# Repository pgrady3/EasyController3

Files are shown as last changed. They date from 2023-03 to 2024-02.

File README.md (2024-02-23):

# EasyController3

*Update Feb 23, 2024 - The EasyController 3.2 has been released, which has been more thoroughly tested than the 3.0. Further tutorial videos and build guides are coming!*

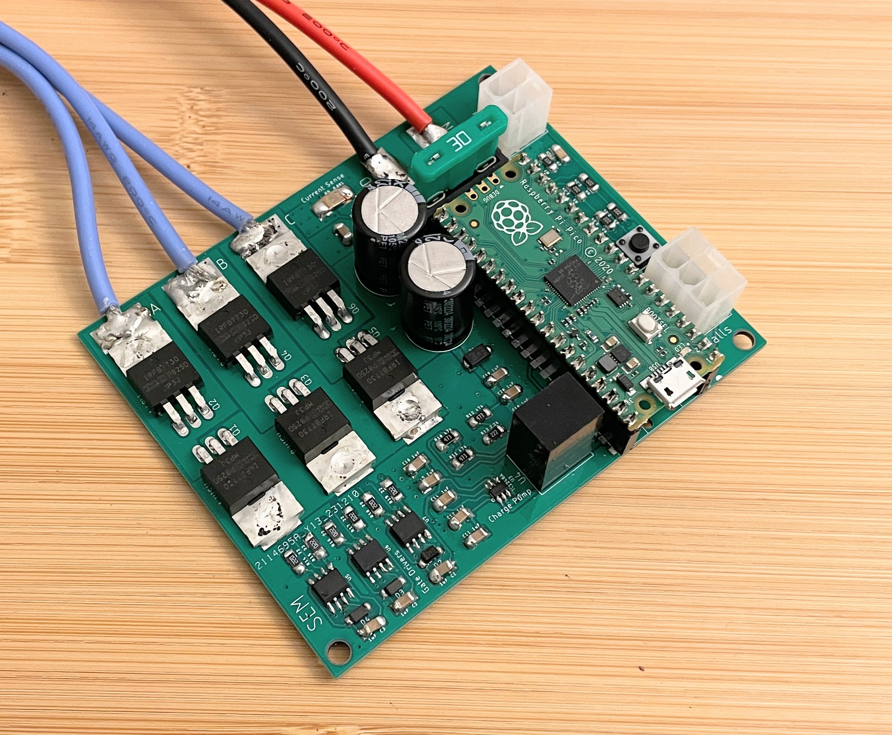
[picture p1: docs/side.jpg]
Assembled Controller


The EasyController3 is the next evolution of the successful [EasyController2](https://github.com/pgrady3/EasyController2). The new version is cheaper, more efficient, and uses well-stocked components.

## Improvements over the EasyController2

* Reduced BOM cost from $70 to $43
* Uses more efficient synchronous PWM. Greater efficiency under partial throttle operation
* Improved from duty-cycle control to torque-control, improving controllability and reducing current spikes
* Added regenerative braking
* Lowered quiescent power from 960 mW to 280 mW in a typical installation
* Based on Raspberry Pi Pico microcontroller
* Uses more widely available surface-mount components

## Getting Started

For a comprehensive guide on how to build your own EasyController, please see the [getting started guide](/docs/getting-started.md).

## Background

The EasyController3 is a a simple brushless (BLDC) sensored motor controller (also known as an ESC, motor inverter, or motor drive). It is intended to power vehicles such as electric bikes, skateboards, or [Eco-Marathon vehicles](https://en.wikipedia.org/wiki/Shell_Eco-marathon) in the 50-1000 watt range. It is designed for hobbyists to assemble at home.

The EasyController family was built to to fill a gap in publicly released motor controller designs. It is designed to be simple yet still highly functional. It deliberately omits more complex features such as sensorless or field-oriented control, however these features can be added with modification. This project is meant as a learning tool and a foundation to potentially build more complex designs from.

## Specifications
* 8v-60v operation
* 20A continuous current, 40A burst (more with heatsinking)
* Large surface mount components designed to be hand-soldered by hobbyists
* Socket for automotive fuse
* Automatic hall sensor identification
* Simple, well-documented code. <400 lines with comments
* Torque or duty-cycle control
* Raspberry Pi Pico microcontroller, compatible with Windows/Mac/Linux
* DGD2304 gate drivers
* IRFB7730 MOSFETS
* BOM cost of $43 USD
* Open source under MIT License

## Schematic

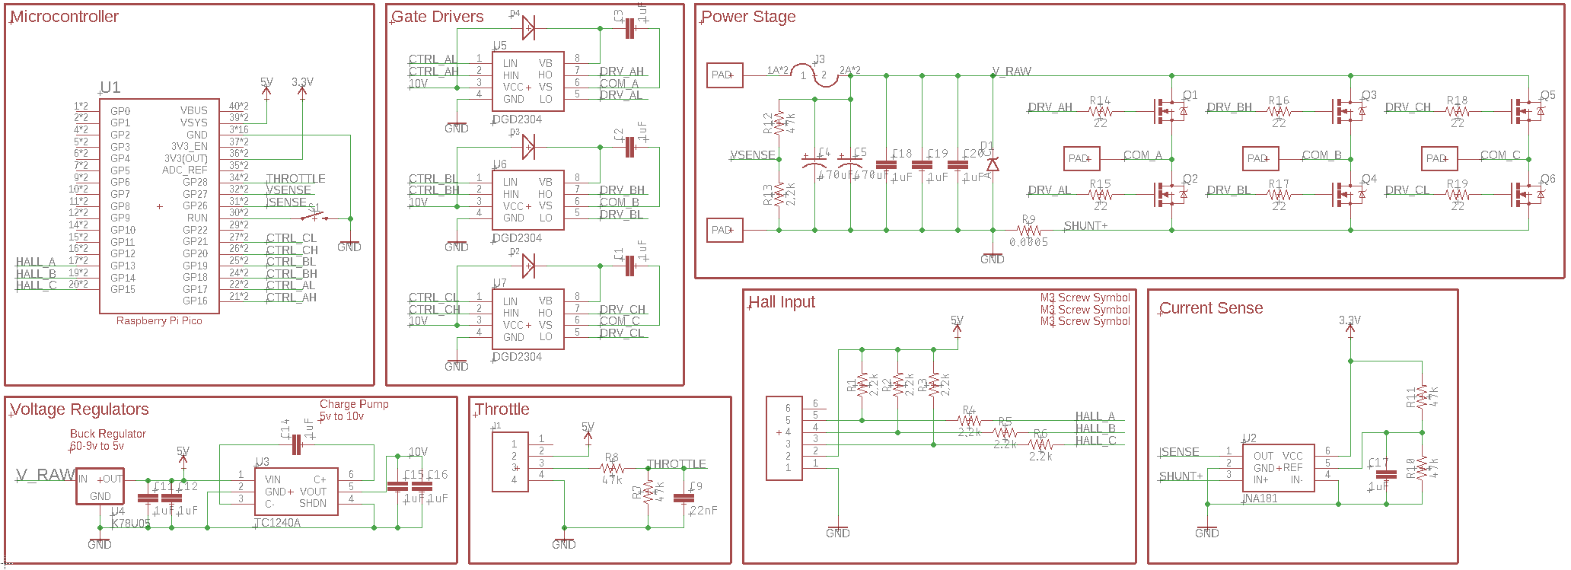
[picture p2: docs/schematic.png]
Schematic


## Board

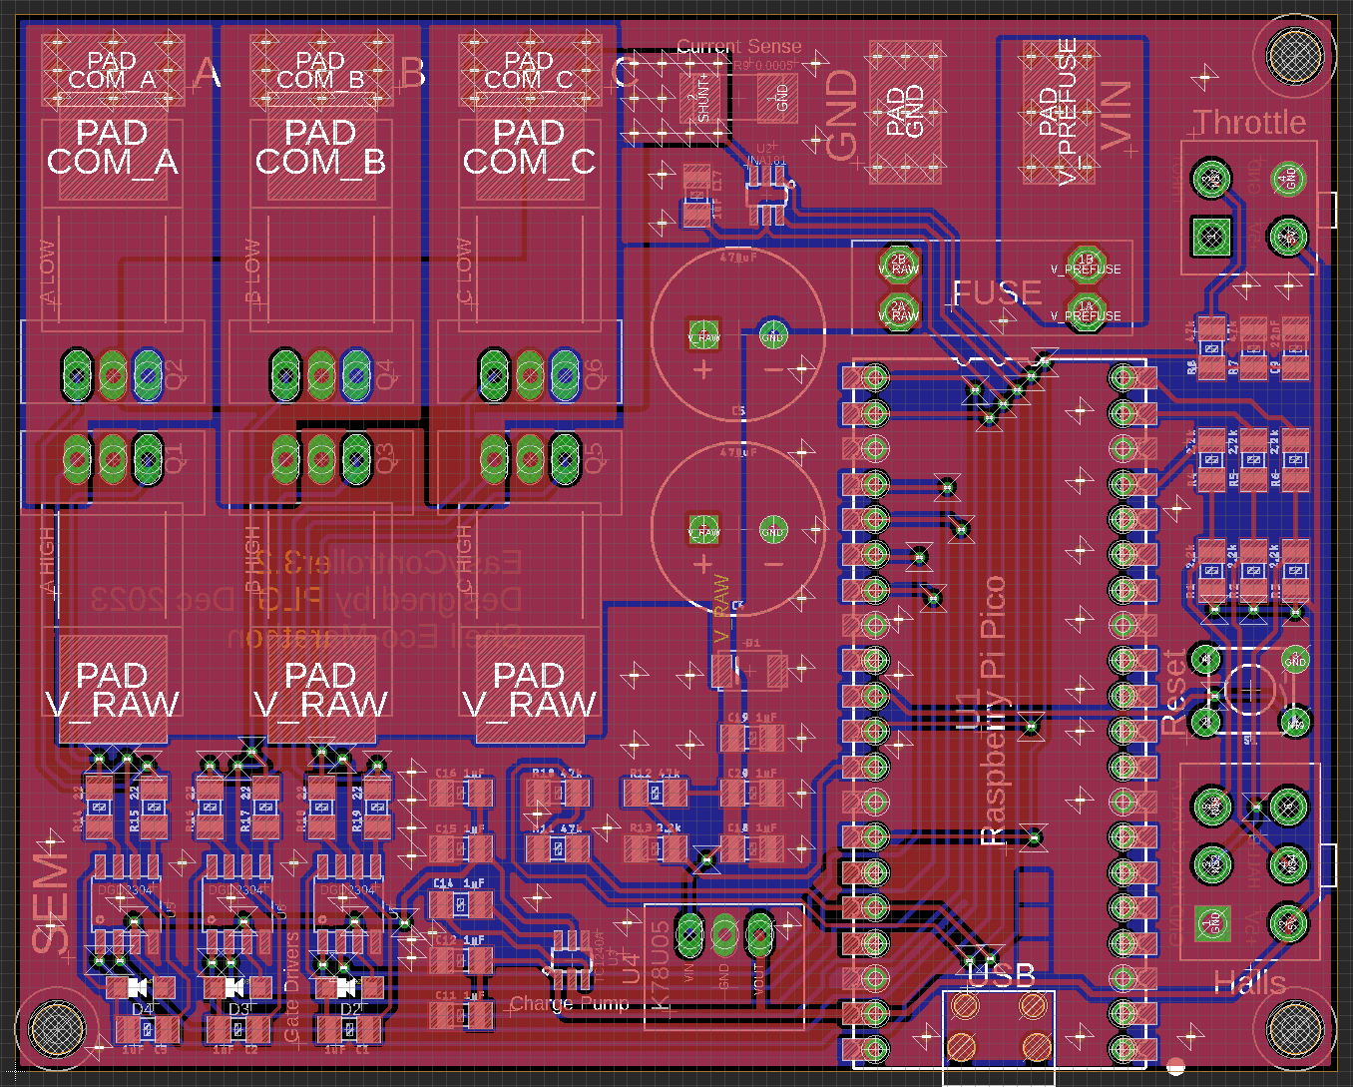
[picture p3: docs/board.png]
Board
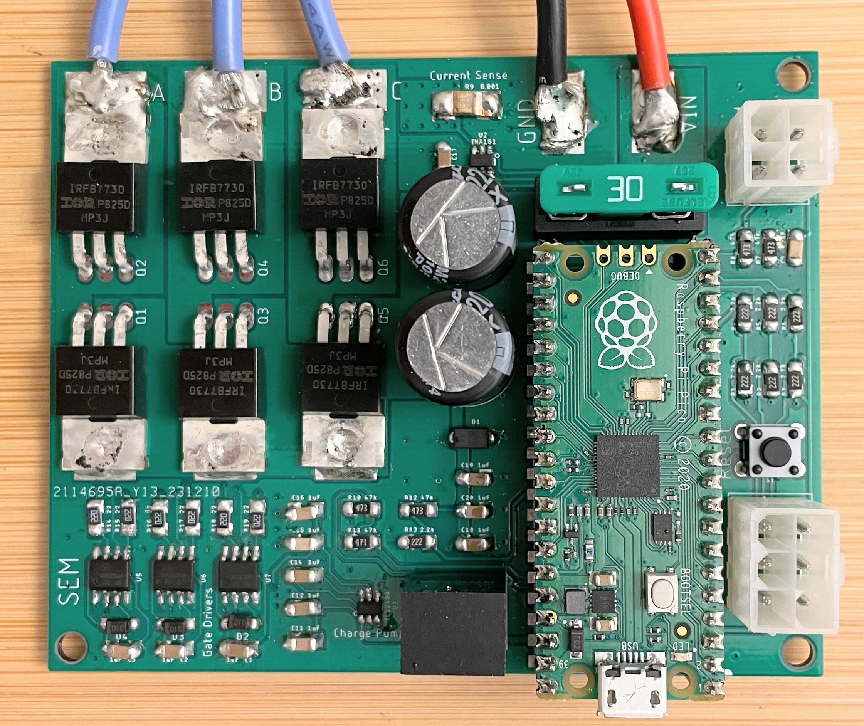
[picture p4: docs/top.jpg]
 

## Software Used

* PCB layout: [Eagle](https://www.autodesk.com/products/eagle/free-download)
* Compiler: [RP2040 C SDK](https://datasheets.raspberrypi.com/pico/getting-started-with-pico.pdf) (see chapter 9)

## Other Related Controller Designs

There are several other open-source motor controller designs worth mentioning:
* The [VESC](https://vesc-project.com/) is a highly capable design, and is well suited for vehicle applications. However, due to the complexity and poorly written code, it is difficult to modify.
* The [Simple FOC](https://simplefoc.com/) project is an open-source library for FOC commutation. However, due to the hardware-agnostic code, it is low-performance and suited for gimbal motors, not vehicle applications.
* The [ODrive](https://odriverobotics.com/) is a modular controller built for robotics applications. However, the hardware is closed-source.

The EasyController3 is most suitable for people who want to design, build, and understand their own motor controller. If you'd just like to purchase something off-the-shelf, we recommend the VESC, which is around $100 USD.

## Contact Us

This controller was designed by [Patrick Grady](https://www.pgrady.net/), formerly with [Duke Electric Vehicles](https://www.duke-ev.org/). If you have a question that other users may also have, please open a GitHub issue. Alternatively, the best way to reach me is by email, at (first name).(last name)@outlook.com.

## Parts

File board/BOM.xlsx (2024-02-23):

Digikey Part # | Mfg Part # | Description | Qty | Cost | Line Cost | Designator | Total Cost
2648-SC0915CT-ND | SC0915 | Raspberry Pi Pico | 1 | 4 | 4 | U1 | 43.15
IRFB7730PBF-ND | IRFB7730PBF | Power FETs | 6 | 3.25 | 19.5 | Q1,Q2,Q3,Q4,Q5,Q6
DGD2304S8-13DICT-ND | DGD2304S8-13 | Gate driver | 3 | 1.26 | 3.78 | U5,U6,U7
SMD110PL-TPMSCT-ND | SMD110PL-TP | Diode for gate driver | 3 | 0.25 | 0.75 | D2,D3,D4
296-INA181A1QDBVRQ1CT-ND | INA181A1 | Current shunt amplifier | 1 | 0.58 | 0.58 | U2
4506-EBWM2512FL500S9CT-ND | EBWM2512FL500S9 | Current shunt resistor | 1 | 0.63 | 0.63 | R9
TC1240AECHCT-ND | TC1240AECHTR | Charge pump IC | 1 | 1.11 | 1.11 | U3
2725-K78U05-500R3-ND | K78U05-500R3 | 5V buck regulator | 1 | 2.89 | 2.89 | U4
1189-3684-ND | 100PX220MEFC12.5X20 | 220uF Capacitor | 2 | 1.14 | 2.28 | C4,C5
SMAJ60CALFCT-ND | SMAJ60CA | TVS Diode | 1 | 0.47 | 0.47 | D1
RMCF1206JT47K0CT-ND | RMCF1206JT47K0 | 47k Resistor | 5 | 0.03 | 0.15 | R7,R8,R10,R11,R12
RMCF1206JT2K20CT-ND | RMCF1206JT2K20 | 2.2k Resistor | 7 | 0.03 | 0.21 | R1,R2,R3,R4,R5,R6,R13
RMCF1206JT22R0CT-ND | RMCF1206JT22R0 | 22 Resistor | 6 | 0.03 | 0.18 | R14,R15,R16,R17,R18,R19
478-12061C223KAT4ACT-ND | 12061C223KAT4A | 22nF Capacitor | 1 | 0.08 | 0.08 | C9
1276-1838-1-ND | CL31B105KCHNNNE | 1uF Capacitor | 13 | 0.19 | 2.47 | C1,C2,C3,C11,C12,C13,C14,C15,C16,C17,C18,C19,C20
36-3557-2-ND | 3557-2 | Fuse holder | 1 | 1.33 | 1.33 | J3
450-1650-ND | 1825910-6 | Reset pushbutton | 1 | 0.13 | 0.13 | S1
A30603-ND | 1586037-4 | 4 pin female VAL-U-LOK | 1 | 0.68 | 0.68 | J1
A30604-ND | 1586037-6 | 6 pin female VAL-U-LOK | 1 | 0.65 | 0.65 | J2
A30591-ND | 794954-4 | 4 pin male VAL-U-LOK | 1 | 0.21 | 0.21
A30592-ND | 794954-6 | 6 pin male VAL-U-LOK | 1 | 0.24 | 0.24
A99267CT-ND | 794956-1 | Crimp pin VAL-U-LOK | 10 | 0.05 | 0.5
F4202-ND | 0287030.PXCN | 30A fuse | 1 | 0.33 | 0.33

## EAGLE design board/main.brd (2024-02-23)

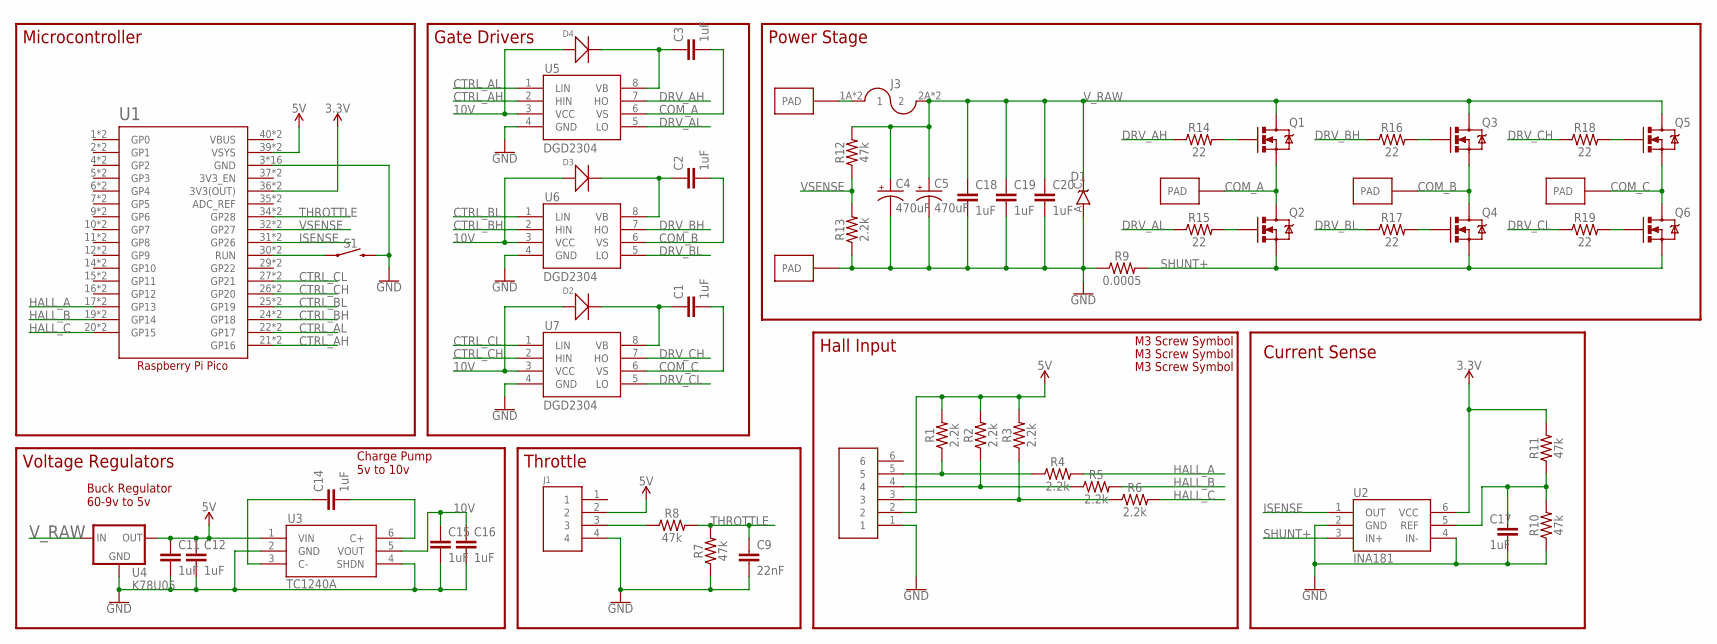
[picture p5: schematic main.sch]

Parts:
C1, C2, C3, C11, C12, C14, C15, C16, C17, C18, C19, C20: 1uF; 1206
C4, C5: 470uF; CPOL-RADIAL-5MM-10MM
C9: 22nF; 1206
D1: TVS; DO-214AC
D2, D3, D4: SMD-DIODE-100V-200MA(SOD-123); SOD-123
J1: HEADER4VALULOK; 4PINVALULOK
J2: HEADER6; 6PINVALULOK
J3: FUSE; AUTO_FUSE
Q1, Q2, Q3, Q4, Q5, Q6: MOSFET-NCHANNELTO-220-FLAT; TO-220-FLAT
R1, R2, R3, R4, R5, R6, R13: 2.2k; 1206
R7, R8, R10, R11, R12: 47k; 1206
R9: 0.0005; R2512
R14, R15, R16, R17, R18, R19: 22; 1206
S1: MOMENTARY-SWITCH-SPST-PTH-6.0MM; TACTILE_SWITCH_PTH_6.0MM
U1: RASPBERRY_PICO-NO_DEBUG; PICO-PKG-NO_DEBUG
U2: INA181; SOT23-6
U3: TC1240A; SOT23-6
U4: K78U05; V78W_BACKWARDS
U5, U6, U7: DGD2304; SOIC8
U$4, U$5, U$6, U$7, U$8: PAD
U$10, U$11, U$12: SCREW; M3HOLE

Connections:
3.3V: R11.2, U1.36 (3V3(OUT)), U1.P$36 (3V3(OUT)), U2.6 (VCC)
5V: C11.1, C12.1, J1.2, J2.2, R1.2, R2.2, R3.2, U1.39 (VSYS), U1.P$39 (VSYS), U3.1 (VIN), U4.OUT
10V: C15.1, C16.1, D2.+, D3.+, D4.+, U3.5 (VOUT), U5.3 (VCC), U6.3 (VCC), U7.3 (VCC)
COM_A: C3.2, Q1.3 (S), Q2.2 (D), Q2.PAD (D), U5.6 (VS), U$6.PAD
COM_B: C2.2, Q3.3 (S), Q4.2 (D), Q4.PAD (D), U6.6 (VS), U$7.PAD
COM_C: C1.2, Q5.3 (S), Q6.2 (D), Q6.PAD (D), U7.6 (VS), U$8.PAD
CTRL_AH: U1.21 (GP16), U1.P$21 (GP16), U5.2 (HIN)
CTRL_AL: U1.22 (GP17), U1.P$22 (GP17), U5.1 (LIN)
CTRL_BH: U1.24 (GP18), U1.P$24 (GP18), U6.2 (HIN)
CTRL_BL: U1.25 (GP19), U1.P$25 (GP19), U6.1 (LIN)
CTRL_CH: U1.26 (GP20), U1.P$26 (GP20), U7.2 (HIN)
CTRL_CL: U1.27 (GP21), U1.P$27 (GP21), U7.1 (LIN)
DRV_AH: R14.1, U5.7 (HO)
DRV_AL: R15.1, U5.5 (LO)
DRV_BH: R16.1, U6.7 (HO)
DRV_BL: R17.1, U6.5 (LO)
DRV_CH: R18.1, U7.7 (HO)
DRV_CL: R19.1, U7.5 (LO)
GND: C4.-, C5.-, C9.2, C11.2, C12.2, C15.2, C16.2, C17.2, C18.2, C19.2, C20.2, D1.A, J1.4, J2.1, R7.1, R9.1, R10.1, R13.1, S1.3 (2), U1.3 (GND), U1.8 (GND), U1.13 (GND), U1.18 (GND), U1.23 (GND), U1.28 (GND), U1.33 (GND), U1.38 (GND), U1.P$3 (GND), U1.P$8 (GND), U1.P$13 (GND), U1.P$18 (GND), U1.P$23 (GND), U1.P$28 (GND), U1.P$33 (GND), U1.P$38 (GND), U2.2 (GND), U2.4 (IN-), U3.2 (GND), U3.4 (SHDN), U4.GND, U5.4 (GND), U6.4 (GND), U7.4 (GND), U$5.PAD
HALL_A: R4.2, U1.17 (GP13), U1.P$17 (GP13)
HALL_B: R5.2, U1.19 (GP14), U1.P$19 (GP14)
HALL_C: R6.2, U1.20 (GP15), U1.P$20 (GP15)
ISENSE: U1.31 (GP26), U1.P$31 (GP26), U2.1 (OUT)
unnamed: C2.1, D3.-, U6.8 (VB)
unnamed: J2.3, R3.1, R6.1
unnamed: C3.1, D4.-, U5.8 (VB)
unnamed: J2.4, R2.1, R5.1
unnamed: Q1.1 (G), R14.2
unnamed: J2.5, R1.1, R4.1
unnamed: J1.3, R8.1
unnamed: C1.1, D2.-, U7.8 (VB)
unnamed: S1.1, U1.30 (RUN), U1.P$30 (RUN)
unnamed: C17.1, R10.2, R11.1, U2.5 (REF)
unnamed: Q2.1 (G), R15.2
unnamed: Q3.1 (G), R16.2
unnamed: Q4.1 (G), R17.2
unnamed: Q5.1 (G), R18.2
unnamed: Q6.1 (G), R19.2
unnamed: C14.1, U3.3 (C-)
unnamed: C14.2, U3.6 (C+)
SHUNT+: Q2.3 (S), Q4.3 (S), Q6.3 (S), R9.2, U2.3 (IN+)
THROTTLE: C9.1, R7.2, R8.2, U1.34 (GP28), U1.P$34 (GP28)
VBUS: U1.40 (VBUS), U1.P$40 (VBUS)
VSENSE: R12.1, R13.2, U1.32 (GP27), U1.P$32 (GP27)
V_PREFUSE: J3.1A (1), J3.1B (1), U$4.PAD
V_RAW: C4.+, C5.+, C18.1, C19.1, C20.1, D1.C, J3.2A (2), J3.2B (2), Q1.2 (D), Q1.PAD (D), Q3.2 (D), Q3.PAD (D), Q5.2 (D), Q5.PAD (D), R12.2, U4.IN

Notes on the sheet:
Power Stage
Hall Input
Gate Drivers
Throttle
Microcontroller
Voltage Regulators
Current Sense
Buck Regulator 60-9v to 5v
Charge Pump 5v to 10v

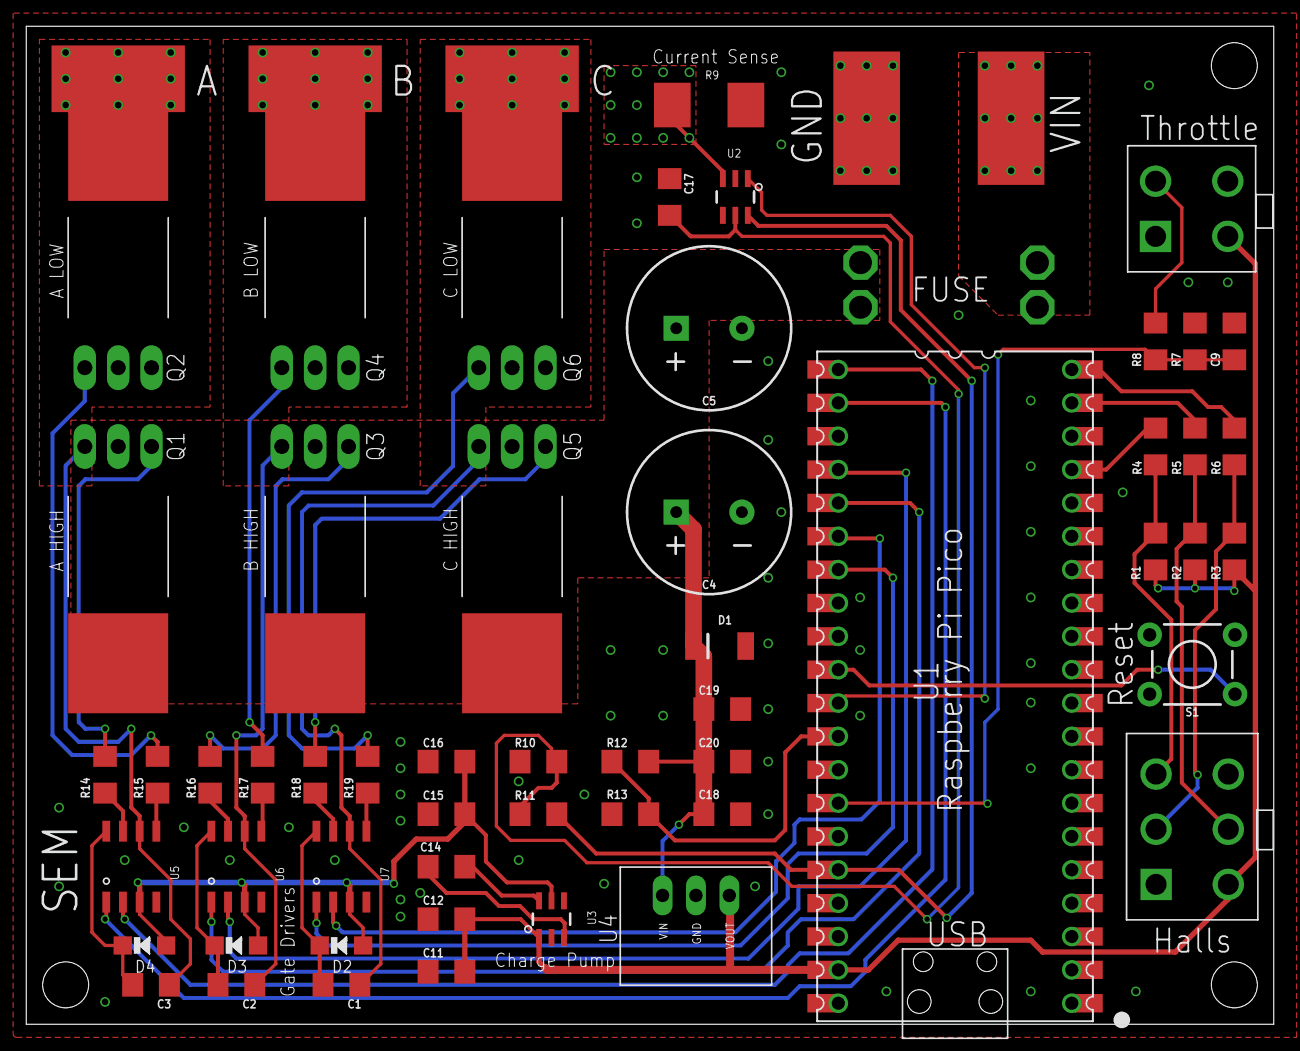
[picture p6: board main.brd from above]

Board: 2 copper layers, 95.0 x 76.0 mm, 63 parts (0 on the bottom side), 46 nets.

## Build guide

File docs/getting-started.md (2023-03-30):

# Building an EasyController3

This document is meant to provide a guide on how to assemble the EasyController3. While some electronics experience is required, hopefully this lowers the barrier to entry.

## What you need

* $100-200 USD to buy parts and boards
* A computer to install the Raspberry Pi Pico SDK on
* A soldering iron and associated tools
* A benchtop power supply capable of ~5 amps for testing
* A BLDC motor 
* A throttle
* High-current wire and connectors for power and motor phase connections
* Low-current wire and connectors for hall sensors and throttle connections

## PCB Manufacturing

This respository includes [Gerber files](/board/gerbers.zip) which can be directly submitted to PCB manufacturers. We recommend Chinese manufacturers such as [JLCPCB](https://jlcpcb.com/), which typically ship worldwide and deliver in one week for $30 USD.

## Buying Components
The repository includes a [Bill of Materials (BOM)](/board/BOM.xlsx) with Digikey part numbers to order from. Digikey ships quickly and internationally. The parts may also be available from other vendors.

Many parts may be substituted, such as resistors, capacitors, and transistors. However, most of the ICs cannot be substituted without changing the design.

## Assembling the Hardware

TODO

## Installing the SDK and Configuring the Firmware

TODO

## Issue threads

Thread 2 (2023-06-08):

Mapping of current and voltage scaling

krishna-1728, 2023-06-08:
We have recently encountered a situation where the board's response to throttle input is unresponsive, with voltage readings remaining stagnant at an oscillation between 0 and 1 volts even when full throttle is applied. After thorough analysis, it has become apparent that there might be a slight discrepancy in the current scaling and voltage synchronization with our motor of choice or there might be an issue with the calibration of the board and motor. It would be helpful if you could suggest a few measures to overcome the issue.

pgrady3, 2023-07-07:
Hey Krishna, that description is helpful, but not quite detailed enough for me to know what's going on. Are you talking about the current control loop?

You can try to manually set the duty cycle and that will always make the motor go.

krishna-1728, 2023-07-07:
The motor is not responding to any input from the throttle because of which it is static. We are not able to figure out what the issue is in the controller. Can you suggest a way to make it work?
What are all things I should consider in the motor controller and make relevant changes to it?
In the previous question I am talking about the output we are getting at all three phases in the motor depending upon the sequence. The range of the output is 0 -1 volts.

pgrady3, 2023-07-07:
Is the controller correctly reading the throttle input from the ADC? You could try printing out the ADC value for the throttle pin.

You can also try attaching a video or photos to give a better sense of what's going on.

krishna-1728, 2023-07-07:
The controller is correctly reading the ADC value from the throttle pin, I have checked it .
Initially, all three phases show 9.8 volts as soon as I give the throttle two phases become zero and the third phase shows variation from 0 -1 volts depending upon the throttle input.

pgrady3, 2023-07-07:
There is a chance the gate drivers are not working properly. I would look to see what duty cycle the controller is outputting, and verify with an oscilloscope if the microcontroller is correctly doing that, and if the gate drivers are correctly doing what they're told.

Sorry, I'm not sure that I can be more of a help without more info.

krishna-1728, 2023-07-07:
Can you please provide me with more detail about the duty cycle it should give, so that I can check that on oscilloscope?
I have created one more speed controller but I am facing issues with the duty cycle and frequency.
 I have attached a copy of the simple code which I have written in Python to control the controller. If you could suggest any changes ?

[Python_code.docx](https://github.com/pgrady3/EasyController3/files/11984897/Python_code.docx)

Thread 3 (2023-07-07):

Regenerative Braking

pirdain, 2023-07-07:
Hey, it says in the Readme that Regenerative Braking was added in the EasyController3 and is an upgrade over the EasyController2, but I'm unable to find any support in the Hardware or Software regarding it. I believe an external circuit would be added to support regenerative braking and supplying current back to the battery pack at the required voltage and this may or may not require some additions in the software (for the basic functionality at least).

If anyone has figured out how to incorporate Regenerative Braking into this project please let me know.

Cheers.

pgrady3, 2023-07-07:
Hi Pirdain,

It's just a software change, and if you set the desired current value negative, the control loop will modulate the duty cycle to make current will flow backwards into the battery. No hardware change is required. However, I haven't tested this yet.

Sorry for the wait, I'm working on the updated 3.1 version that will have this feature enabled and tested.

Patrick

pirdain, 2023-07-10:
Hey Patrick,

Thanks for the quick response. I'll test this with my motor and get back with the results.

Also I had another question, how do I calculate the Capacitance value for the Capacitor Bank. Did you follow some formula for it. The provided value is as per a lower wattage motor, 1 kW. The motor in my circuit is around 5 - 6 kW.

I understand that the Issue is for Regenerative Braking and this would need another issue altogether, but still any input is appreciated.

Kind Regards,
Pirdain

pgrady3, 2023-07-10:
Hey Pirdain,

Choosing these bypass capacitors is a very empirical process. I'd recommend finding a comparable 5 kW controller, and just copying the capacitance value from that. Alternatively, you could design in 5x more capacitance, and solder in different values depending on what you find when testing.

Patrick

bmentink, 2024-04-09:
Just a point regarding managing regen energy. If the current limit to the battery is set too low, or the battery won't accept any more current (fully charged), the regen voltage may still rise to a damaging level. One way around that is to dump to an external high power resistor in that situation.

Maybe that could be added to version4 ;)

pgrady3, 2024-04-11:
Yes, some controllers have a shunt resistor for these kinds of applications. I think this is mostly used for industrial BLDC servos, where dumping energy back into the bus is unacceptable.

On most vehicle applications (what this controller is really built for), you apply the mechanical brakes if the controller can't regen. And usually, the battery's stored energy is much larger than the kinetic energy of the vehicle, so over-charging the battery isn't a concern.

However, you're welcome to add more features to the design!

bmentink, 2024-04-19:
Hi Patrick,

I am making great progress with sensorless addition to easycontroller3. The
zero-cross detection is achieved with simple (two resistors and a fet)
components  per phase. I have used a majority filter function in software
to clean it up, works great between 18v and 48v, no hardware filtering at
all, just straight into the ADC.

Attached is a scope shot.

Cheers,
Bernard

On Thu, Apr 11, 2024 at 5:53 PM Patrick Grady ***@***.***>
wrote:

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

bmentink, 2024-05-17:
Hi Patrick,

I have finally managed to get an implementation of sensorless operation
working on your board. It works reliably over a voltage range of 12v to 48v
with no hardware changes needed to support different voltages, I can just
ramp up the bench power supply to whatever voltage. And it starts up
reliably , even under load.

I can't stop the motor by loading the shaft with my hand, but will need
real load testing.

The hardware involved is 3 small signal fet',s a bunch of resistors and the
CD4051 mux .. (finally got that working correctly) so would
not be much to add to the bottom of the board.

At the moment, for development, I have totally re-written your software to
support this mode, and I have yet to add back current/torque control. (Also
it is written in Forth, not C, because it was fast to test out code for
development) When I am totally happy with it I could port it back to C ...

Just thought I would keep you up to date  with the development.

Cheers,
Bernie

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

Closed 2024-04-11.

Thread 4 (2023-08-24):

Version 3.1

samuk, 2023-08-24:
Is the new version still planned?

krekr, 2023-10-01:
I’m watching this also. If the fix can be described, that would help as well. Thanks!

samuk, 2023-10-01:
Yes that might help. @pgrady3 could you describe the problem?

TinkerGear, 2023-10-08:
A description of the problem would be very helpful to us as well!

pgrady3, 2023-10-09:
Hi all, apologies for the slow reply. I'm pretty busy here finishing up with my PhD, hence the slow progress. Adding a 22 ohm resistor between the transistor gate and the gate drivers fixes the problem of the gate drivers blowing up.

However, there were a few other issues that I've also been working on:

- The components are a bit too hard to solder, and determining the orientation of the SOT-23-6's is almost impossible. I'm switching them out for bigger components
- The code is a mess. It needs to be cleaned up and
- I think the gate driver deadtime is too short, and the transistors heat up a too much during operation.

Apologies on the buggy release. I rushed this one, and as a result it's not very polished.

krekr, 2023-10-09:
Thanks very much. This gives me enough confidence to fork it and design a smaller version that fits into a certain application.

samuk, 2023-10-16:
@krekr I'd be interested in checking out your fork if you could post it here.

krekr, 2024-02-23:
Huzzah for v3.2! Thanks @pgrady3

Closed 2024-02-23.

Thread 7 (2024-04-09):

Converted PCB files to Kicad

bmentink, 2024-04-09:
Just thought I'd tell you that the Eagle files converted quite easily to Kicad that most people use now.
I can send you the project files if required, then you could share those as well ..

l4m4re, 2024-07-15:
Would be interested in those. I also converted the Eagle files to Kicad, but there were a few problems in the design rule checker I don't yet know how to fix.

If you are willing to share, please put them up on wetransfer or something and drop the link here in the discussion.

bmentink, 2024-07-15:
I ignored the errors, as they are just because the tolerances are different on Eagle. It will build fine ...

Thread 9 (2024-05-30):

BLDC Hall sensors output 5v - should this be divided for the pi pico?

joshmcculloch, 2024-05-30:
Hello,

I have been doing some testing and the driver is preforming well. I was a bit concerned to see 5v on the hall input pins. Do we need to add a resistor divider to the design. Or is it unusual for the hall logic output to be 5v? I see some of the hall sensors support 3.3-5v, so another option might be to power them from the pico's 3v3 rail.

Also happy to hear that I'm wrong and this is a non issue.

joshmcculloch, 2024-05-30:
Follow up. It seems that hall effects are generally open collector - mine are. So the solution I'm going to try is breaking the 5v pull up line along the edge of the board and connecting it to the pi's 3v3 via the R3 pad.

l4m4re, 2024-07-15:
In my design (still in progress) for a controller with an asymmetric bridge, I opted for ISO7760FQDWRQ1 isolated buffers:

https://github.com/l4m4re/BEMF_Controller/blob/main/kicad/BEMF_controller.pdf

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

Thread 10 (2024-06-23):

My version of the controller that is now sensorless ..

bmentink, 2024-06-23:
Did a version of the board (in Kicad) that does sensorless, all that was added is 3 small high voltage fet's and a bunch of caps/resistors.

See attached photo .. motor runs well at full torque from 100rpm to max rated (4000 for this motor).
I have not obtained a higher KV motor to test at higher rpm'3 yet ..

The motor can run from 12v to 48v (In fact you can adjust the voltage while the motor is running, and it does not miss a beat, as the sensorless circuit copes with it ..)
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

By the way the DC/DC Converter you specified is no longer available. In the picture I have a temporary larger one attached for testing.

bmentink, 2024-06-27:
Update: I have tried my sensorless version on 4 motors now, all different sizes and KV ratings. It all just works, you don't have to calibrate anything, just attach the motor and go ..

bmentink, 2024-07-04:
And here is the adapter board running a RP2040-Zero
![Uploading IMG_20240705_113932025.jpg…]()

emstraske, 2025-01-16:
Hello, would it be possible for you to share the board files and code for the sensorless version of the controller? I’d love to study and learn from your implementation. However, I understand if you prefer to keep it private.

Thank you for sharing your progress, and I look forward to any insights you're willing to share!

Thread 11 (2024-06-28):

Designators missing

FMullerR, 2024-06-28:
My name is Francisco Muller, and I lead the Shell Eco-Marathon team at Universidad Panamericana in Mexico. This is our first year competing in the Shell Eco-Marathon, and we've hit a few snags with the motor controller for our electric vehicle.

Our team is made up entirely of first-year engineering students, so there are a lot of things we're still learning. Your EasyController3 project has been our main resource of guidance, but we're facing some issues as we move forward.

We've decided to have our motor controller printed and assembled in China due to our lack of experience and tight deadlines. However, when preparing the documentation for the components, we noticed that some of them don't have a designator. This left us with some questions.

We would be extremely grateful if you could help us figure out if we've missed something important or misunderstood part of the documentation. Your guidance would be incredibly valuable to us in making sure our controller is properly manufactured and functional.
[T-2C2W717754A-5sets-Sample_BOM_PCBWay(2024-06-13) (1).xls](https://github.com/user-attachments/files/16033720/T-2C2W717754A-5sets-Sample_BOM_PCBWay.2024-06-13.1.xls)

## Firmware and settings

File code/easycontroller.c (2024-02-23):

#include <stdio.h>
#include "pico/stdlib.h"
#include "hardware/pwm.h"
#include "hardware/clocks.h"
#include "hardware/irq.h"
#include "hardware/adc.h"
#include "hardware/gpio.h"
#include "hardware/sync.h"
#include "hardware/uart.h"

// Begin user config section ---------------------------

const bool IDENTIFY_HALLS_ON_BOOT = true;   // If true, controller will initialize the hall table by slowly spinning the motor
const bool IDENTIFY_HALLS_REVERSE = false;  // If true, will initialize the hall table to spin the motor backwards

uint8_t hallToMotor[8] = {255, 255, 255, 255, 255, 255, 255, 255};  // Default hall table. Overwrite this with the output of the hall auto-identification 
// uint8_t hallToMotor[8] = {255, 2, 0, 1, 4, 3, 5, 255};  // Example hall table

const int THROTTLE_LOW = 600;               // ADC value corresponding to minimum throttle, 0-4095
const int THROTTLE_HIGH = 2650;             // ADC value corresponding to maximum throttle, 0-4095

const bool CURRENT_CONTROL = true;          // Use current control or duty cycle control
const int PHASE_MAX_CURRENT_MA = 6000;      // If using current control, the maximum phase current allowed
const int BATTERY_MAX_CURRENT_MA = 3000;    // If using current control, the maximum battery current allowed
const int CURRENT_CONTROL_LOOP_GAIN = 200;  // Adjusts the speed of the current control loop

// End user config section -----------------------------

const uint LED_PIN = 25;
const uint AH_PIN = 16;
const uint AL_PIN = 17;
const uint BH_PIN = 18;
const uint BL_PIN = 19;
const uint CH_PIN = 20;
const uint CL_PIN = 21;
const uint HALL_1_PIN = 13;
const uint HALL_2_PIN = 14;
const uint HALL_3_PIN = 15;
const uint ISENSE_PIN = 26;
const uint VSENSE_PIN = 27;
const uint THROTTLE_PIN = 28;

const uint A_PWM_SLICE = 0;
const uint B_PWM_SLICE = 1;
const uint C_PWM_SLICE = 2;

const uint F_PWM = 16000;   // Desired PWM frequency
const uint FLAG_PIN = 2;
const uint HALL_OVERSAMPLE = 8;

const int DUTY_CYCLE_MAX = 65535;
const int CURRENT_SCALING = 3.3 / 0.0005 / 20 / 4096 * 1000;
const int VOLTAGE_SCALING = 3.3 / 4096 * (47 + 2.2) / 2.2 * 1000;
const int ADC_BIAS_OVERSAMPLE = 1000;

const int HALL_IDENTIFY_DUTY_CYCLE = 25;

int adc_isense = 0;
int adc_vsense = 0;
int adc_throttle = 0;

int adc_bias = 0;
int duty_cycle = 0;
int voltage_mv = 0;
int current_ma = 0;
int current_target_ma = 0;
int hall = 0;
uint motorState = 0;
int fifo_level = 0;
uint64_t ticks_since_init = 0;

uint get_halls();
void writePWM(uint motorState, uint duty, bool synchronous);
uint8_t read_throttle();


void on_adc_fifo() {
    // This interrupt is where the magic happens. This is fired once the ADC conversions have finished (roughly 6us for 3 conversions)
    // This reads the hall sensors, determines the motor state to switch to, and reads the current sensors and throttle to
    // determine the desired duty cycle. This takes ~7us to complete.

    uint32_t flags = save_and_disable_interrupts(); // Disable interrupts for the time-critical reading ADC section. USB interrupts may interfere

    adc_run(false);             // Stop the ADC from free running
    gpio_put(FLAG_PIN, 1);      // For debugging, toggle the flag pin

    fifo_level = adc_fifo_get_level();
    adc_isense = adc_fifo_get();    // Read the ADC values into the registers
    adc_vsense = adc_fifo_get();
    adc_throttle = adc_fifo_get();

    restore_interrupts(flags);      // Re-enable interrupts

    if(fifo_level != 3) {
        // The RP2040 is a shitty microcontroller. The ADC is unpredictable, and 1% of times
        // will return more or less than the 3 samples it should. If we don't get the expected number, abort
        return;
    }

    hall = get_halls();                 // Read the hall sensors
    motorState = hallToMotor[hall];     // Convert the current hall reading to the desired motor state

    int throttle = ((adc_throttle - THROTTLE_LOW) * 256) / (THROTTLE_HIGH - THROTTLE_LOW);  // Scale the throttle value read from the ADC
    throttle = MAX(0, MIN(255, throttle));      // Clamp to 0-255

    current_ma = (adc_isense - adc_bias) * CURRENT_SCALING;     // Since the current sensor is bidirectional, subtract the zero-current value and scale
    voltage_mv = adc_vsense * VOLTAGE_SCALING;  // Calculate the bus voltage

    if(CURRENT_CONTROL) {
        int user_current_target_ma = throttle * PHASE_MAX_CURRENT_MA / 256;  // Calculate the user-demanded phase current
        int battery_current_limit_ma = BATTERY_MAX_CURRENT_MA * DUTY_CYCLE_MAX / duty_cycle;  // Calculate the maximum phase current allowed while respecting the battery current limit
        current_target_ma = MIN(user_current_target_ma, battery_current_limit_ma);

        if (throttle == 0)
        {
            duty_cycle = 0;     // If zero throttle, ignore the current control loop and turn all transistors off
            ticks_since_init = 0;   // Reset the timer since the transistors were turned on
        }
        else
            ticks_since_init++;

        duty_cycle += (current_target_ma - current_ma) / CURRENT_CONTROL_LOOP_GAIN;  // Perform a simple integral controller to adjust the duty cycle
        duty_cycle = MAX(0, MIN(DUTY_CYCLE_MAX, duty_cycle));   // Clamp the duty cycle

        bool do_synchronous = ticks_since_init > 16000;    // Only enable synchronous switching some time after beginning control loop. This allows control loop to stabilize
        writePWM(motorState, (uint)(duty_cycle / 256), do_synchronous);
    }
    else {
        duty_cycle = throttle * 256;    // Set duty cycle based directly on throttle
        bool do_synchronous = true;     // Note, if doing synchronous duty-cycle control, the motor will regen if the throttle decreases. This may regen VERY HARD

        writePWM(motorState, (uint)(duty_cycle / 256), do_synchronous);
    }

    gpio_put(FLAG_PIN, 0);
}

void on_pwm_wrap() {
    // This interrupt is triggered when the A_PWM slice reaches 0 (the middle of the PWM cycle)
    // This allows us to start ADC conversions while the high-side FETs are on, which is required
    // to read current, based on where the current sensor is placed in the schematic.
    // Takes ~1.3 microseconds

    gpio_put(FLAG_PIN, 1);      // Toggle the flag pin high for debugging
    adc_select_input(0);        // Force the ADC to start with input 0
    adc_run(true);              // Start the ADC
    pwm_clear_irq(A_PWM_SLICE); // Clear this interrupt flag
    while(!adc_fifo_is_empty()) // Clear out the ADC fifo, in case it still has samples in it
        adc_fifo_get();

    gpio_put(FLAG_PIN, 0);
}

void writePhases(uint ah, uint bh, uint ch, uint al, uint bl, uint cl)
{
    // Set the timer registers for each PWM slice. The lowside values are inverted,
    // since the PWM slices were already configured to invert the lowside pin.
    // ah: desired high-side duty cycle, range of 0-255
    // al: desired low-side duty cycle, range of 0-255

    pwm_set_both_levels(A_PWM_SLICE, ah, 255 - al);
    pwm_set_both_levels(B_PWM_SLICE, bh, 255 - bl);
    pwm_set_both_levels(C_PWM_SLICE, ch, 255 - cl);
}

void writePWM(uint motorState, uint duty, bool synchronous)
{
    // Switch the transistors given a desired electrical state and duty cycle
    // motorState: desired electrical position, range of 0-5
    // duty: desired duty cycle, range of 0-255
    // synchronous: perfom synchronous (low-side and high-side alternating) or non-synchronous switching (high-side only) 

    if(duty == 0 || duty > 255)     // If zero throttle, turn both low-sides and high-sides off
        motorState = 255;

    // At near 100% duty cycles, the gate driver bootstrap capacitor may become discharged as the high-side gate is repeatedly driven
    // high and low without time for the phase voltage to fall to zero and charge the bootstrap capacitor. Thus, if duty cycle is near
    // 100%, clamp it to 100%.
    if(duty > 245)
        duty = 255;

    uint complement = 0;
    if(synchronous)
    {
        complement = MAX(0, 248 - (int)duty);    // Provide switching deadtime by having duty + complement < 255
    }

    if(motorState == 0)                         // LOW A, HIGH B
        writePhases(0, duty, 0, 255, complement, 0);
    else if(motorState == 1)                    // LOW A, HIGH C
        writePhases(0, 0, duty, 255, 0, complement);
    else if(motorState == 2)                    // LOW B, HIGH C
        writePhases(0, 0, duty, 0, 255, complement);
    else if(motorState == 3)                    // LOW B, HIGH A
        writePhases(duty, 0, 0, complement, 255, 0);
    else if(motorState == 4)                    // LOW C, HIGH A
        writePhases(duty, 0, 0, complement, 0, 255);
    else if(motorState == 5)                    // LOW C, HIGH B
        writePhases(0, duty, 0, 0, complement, 255);
    else                                        // All transistors off
        writePhases(0, 0, 0, 0, 0, 0);
}

void init_hardware() {
    // Initialize all peripherals

    stdio_init_all();

    gpio_init(LED_PIN);     // Set LED and FLAG pin as outputs
    gpio_set_dir(LED_PIN, GPIO_OUT);
    gpio_init(FLAG_PIN);
    gpio_set_dir(FLAG_PIN, GPIO_OUT);

    gpio_init(HALL_1_PIN);  // Set up hall sensor pins
    gpio_set_dir(HALL_1_PIN, GPIO_IN);
    gpio_init(HALL_2_PIN);
    gpio_set_dir(HALL_2_PIN, GPIO_IN);
    gpio_init(HALL_3_PIN);
    gpio_set_dir(HALL_3_PIN, GPIO_IN);

    gpio_set_function(AH_PIN, GPIO_FUNC_PWM);   // Set gate control pins as output
    gpio_set_function(AL_PIN, GPIO_FUNC_PWM);
    gpio_set_function(BH_PIN, GPIO_FUNC_PWM);
    gpio_set_function(BL_PIN, GPIO_FUNC_PWM);
    gpio_set_function(CH_PIN, GPIO_FUNC_PWM);
    gpio_set_function(CL_PIN, GPIO_FUNC_PWM);

    adc_init();
    adc_gpio_init(ISENSE_PIN);  // Set up ADC pins
    adc_gpio_init(VSENSE_PIN);
    adc_gpio_init(THROTTLE_PIN);

    sleep_ms(100);
    for(uint i = 0; i < ADC_BIAS_OVERSAMPLE; i++)   // Find the zero-current ADC reading. Reads the ADC multiple times and takes the average
    {
        adc_select_input(0);
        adc_bias += adc_read();
    }
    adc_bias /= ADC_BIAS_OVERSAMPLE;

    adc_set_round_robin(0b111);     // Set ADC to read our three ADC pins one after the other (round robin)
    adc_fifo_setup(true, false, 3, false, false);   // ADC writes into a FIFO buffer, and an interrupt is fired once FIFO reaches 3 samples
    irq_set_exclusive_handler(ADC_IRQ_FIFO, on_adc_fifo);   // Sets ADC interrupt
    irq_set_priority(ADC_IRQ_FIFO, 0);
    adc_irq_set_enabled(true);
    irq_set_enabled(ADC_IRQ_FIFO, true);

    pwm_clear_irq(A_PWM_SLICE);     // Clear interrupt flag, just in case
    irq_set_exclusive_handler(PWM_IRQ_WRAP, on_pwm_wrap);   // Set interrupt to fire when PWM counter wraps
    irq_set_priority(PWM_IRQ_WRAP, 0);
    irq_set_enabled(PWM_IRQ_WRAP, true);

    float pwm_divider = (float)(clock_get_hz(clk_sys)) / (F_PWM * 255 * 2);     // Calculate the desired PWM divisor
    pwm_config config = pwm_get_default_config();
    pwm_config_set_clkdiv(&config, pwm_divider);
    pwm_config_set_wrap(&config, 255 - 1);      // Set the PWM to wrap at 254. This allows a PWM value of 255 to equal 100% duty cycle
    pwm_config_set_phase_correct(&config, true);    // Set phase correct (counts up then down). This is allows firing the interrupt in the middle of the PWM cycle
    pwm_config_set_output_polarity(&config, false, true);   // Invert the lowside PWM such that 0 corresponds to lowside transistors on

    writePhases(0, 0, 0, 0, 0, 0);  // Initialize all the PWMs to be off

    pwm_init(A_PWM_SLICE, &config, false);
    pwm_init(B_PWM_SLICE, &config, false);
    pwm_init(C_PWM_SLICE, &config, false);

    pwm_set_mask_enabled(0x07); // Enable our three PWM timers
}

uint get_halls() {
    // Read the hall sensors with oversampling. Hall sensor readings can be noisy, which produces commutation "glitches".
    // This reads the hall sensors multiple times, then takes the majority reading to reduce noise. Takes ~200 nanoseconds

    uint hallCounts[] = {0, 0, 0};
    for(uint i = 0; i < HALL_OVERSAMPLE; i++) // Read all the hall pins repeatedly, count votes
    {
        hallCounts[0] += gpio_get(HALL_1_PIN);
        hallCounts[1] += gpio_get(HALL_2_PIN);
        hallCounts[2] += gpio_get(HALL_3_PIN);
    }

    uint hall_raw = 0;
    for(uint i = 0; i < 3; i++)
        if (hallCounts[i] > HALL_OVERSAMPLE / 2)    // If more than half the readings are positive,
            hall_raw |= 1<<i;                       // set the i-th bit high

    return hall_raw;    // Range is 0-7. However, 0 and 7 are invalid hall states
}

void identify_halls()
{
    // This is the magic function which sets the hallToMotor commutation table. This allows
    // you to plug in the motor and hall wires in any order, and the controller figures out the order.
    // This works by PWM-ing to all of the "half states", such as 0.5, by switching rapidly between state 0 and 1.
    // This commutates to all half-states and reads the corresponding hall value. Then, since electrical position
    // should lead rotor position by 90 degrees, for this hall state, save a motor state 1.5 steps ahead.

    sleep_ms(2000);
    for(uint i = 0; i < 6; i++)
    {
        for(uint j = 0; j < 1000; j++)       // Commutate to a half-state long enough to allow the rotor to stop moving
        {
            sleep_us(500);
            writePWM(i, HALL_IDENTIFY_DUTY_CYCLE, false);
            sleep_us(500);
            writePWM((i + 1) % 6, HALL_IDENTIFY_DUTY_CYCLE, false);     // PWM to the next half-state
        }

        if(IDENTIFY_HALLS_REVERSE)
            hallToMotor[get_halls()] = (i + 5) % 6;     // If the motor should spin backwards, save a motor state of -1.5 steps
        else
            hallToMotor[get_halls()] = (i + 2) % 6;     // If the motor should spin forwards, save a motor state of +1.5 steps
    }

    writePWM(0, 0, false);      // Turn phases off

    printf("hallToMotor array:\n");     // Print out the array
    for(uint8_t i = 0; i < 8; i++)
        printf("%d, ", hallToMotor[i]);
    printf("\nIf any values are 255 except the first and last, auto-identify failed. Otherwise, save this table in code.\n");
}

void commutate_open_loop()
{
    // A useful function to debug electrical problems with the board.
    // This slowly advances the motor commutation without reading hall sensors. The motor should slowly spin
    int state = 0;
    while(true)
    {
        writePWM(state % 6, 25, false);
        sleep_ms(50);
        state++;
    }
}

int main() {
    init_hardware();

    // commutate_open_loop();   // May be helpful for debugging electrical problems

    if(IDENTIFY_HALLS_ON_BOOT)
        identify_halls();

    sleep_ms(1000);

    pwm_set_irq_enabled(A_PWM_SLICE, true); // Enables interrupts, starting motor commutation

    while (true) {
        printf("%6d, %6d, %6d, %6d, %2d, %2d\n", current_ma, current_target_ma, duty_cycle, voltage_mv, hall, motorState);
        gpio_put(LED_PIN, !gpio_get(LED_PIN));  // Toggle the LED
        sleep_ms(100);
    }

    return 0;
}

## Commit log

2023-03-30 Synchronous current-control works
2023-03-30 Initial commit of docs
    [BOM.xlsx]
2023-05-12 Updated readme, gate driver fix in works
2023-12-05 Pointone update
    [BOM.xlsx, main.brd, main.sch]
2023-12-11 3.2 initial commit, changed FETs to TO-220s
    [BOM.xlsx, main.brd, main.sch]
2024-02-19 Code works
    [main.brd, main.sch]
2024-02-23 Cleaned up code, added tons of comments
    [main.brd]
2024-02-23 Updated BOM
    [BOM.xlsx]
2024-02-23 Updated gerbers, docs, and images

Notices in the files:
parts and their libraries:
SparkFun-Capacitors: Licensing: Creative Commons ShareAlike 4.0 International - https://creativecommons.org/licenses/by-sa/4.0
